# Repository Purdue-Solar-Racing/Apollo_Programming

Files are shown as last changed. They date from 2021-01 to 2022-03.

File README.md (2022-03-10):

# Apollo_Programming
Purdue Solar main code repository for the Apollo car. 

## Subsystem Hardware Status
Status Key and Due Dates
0. Not Started
1. Started in Research
2. In Schematic Work
3. Schematic Finished - Oct 23rd, 2021
4. PCB Layout Finished - Nov 13/20th, 2021
5. Manufactuing Stage
6. Debugged and Working

| Subsystem | Lead | Status | Members | Notes |
|---|---|---|---|---|
| Battery Protection System | Nate Nauman | 2/3 | Nicholas Gildenhuys | |
| Driver Display | Rachael Getz | 1 | Darin Tsai, Jing Hoon | |
| Light Controller | Darin Tsai | 3 | | |
| Junction Controller | Nicholas Gildenhuys | 0 | | |
| Motor Controller | Nate Nauman | 2 | Nicholas Gildenhuys | |
| Solar Array Controller | Landon Lindsay | 3 | Dhanu De Silva, Jing Hoon | |
| Vehicle Controller | Roshni Sharma | 2/3 | | |
| Wheel Controller | Nicholas Gildenhuys | 3 | | |

## Subsystem Software Status
Status Key:
0. Not Started
1. Started in Research
2. Prelim Code
3. Main Functions Built Out
4. Integration Stage
5. Integration Finished

| Subsystem | Lead | Status | Members | Notes |
|---|---|---|---|---|
| Battery Protection System | | 0 | 			 | |
| Driver Display | 			 | 0 | | |
| Light Controller | 		 | 0 | | |
| Junction Controller | 			 | 0 | | |
| Motor Controller | 		 | 0 | 			 | |
| Solar Array Controller | 		 | 0 | 			 | |
| Vehicle Controller | 		 | 0 | | |
| Wheel Controller | 			 | 0 | | |

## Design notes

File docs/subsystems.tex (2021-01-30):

\documentclass[letterpaper,12pt]{article}
\usepackage{amsmath, amssymb, geometry, amsfonts, graphicx}
\graphicspath{{./}}
\usepackage[shortlabels]{enumitem}
\usepackage{multicol}
\usepackage{hyperref}

\geometry{left=1in, right=1in, top=1in, bottom=1in}

\title{Purdue Solar Racing Apollo Electrical Susystems}
\author{Nicholas Gildenhuys}
\begin{document}

\maketitle
\tableofcontents
\newpage

\section{Battery Protection Controller}
   Main Function: Protect batteries and relay information fo the telemetry and driver display boards.  
   \subsection{Board I/O}
   \begin{multicols}{2}
   \flushleft{\textbf{Inputs:}}
   
   \flushleft{CAN:}
   \begin{itemize}
      \item Init Startup
   \end{itemize}
      
   \flushleft{Hardware:}
   \begin{itemize}
      \item Battery terminals
      \item Thermal sensor
      \item Voltage Sensor
      \item Aux Voltage
   \end{itemize}
   
   \columnbreak
   
   \flushleft{\textbf{Outputs:}}

   \flushleft{CAN:}
   \begin{itemize}
      \item Board Ready
      \item Battery Themperature
      \item Battery Capacity
   \end{itemize}
   
   \flushleft{Hardware:}
   \begin{itemize}
      \item Protected battery output
   \end{itemize}
   \end{multicols}
   % ARM-Cortex M1 Chip needed inputs and outputs
   \subsection{Processor Ports}
   \begin{multicols}{2}
   \begin{enumerate}[(a.)]
      \item power/ground
      \item CAN I/O network ports
      \item \# of thermistors
      \item \# Voltage info from IC
      
      \item CAN status
   \end{enumerate}
   \end{multicols}

\pagebreak
\section{Driver Display}
Main Function: Display all necessary info to the driver.
   \subsection{Board I/O}
   \begin{multicols}{2}
   \flushleft{\textbf{Inputs:}}
   
   \flushleft{CAN:}
   \begin{itemize}
      \item Init Startup
      \item All car signals
   \end{itemize}
   
   \flushleft{Hardware:}
   \begin{itemize}
      \item Aux Voltage
   \end{itemize}
   
   \columnbreak
   
   \flushleft{\textbf{Outputs:}}

   \flushleft{CAN:}
   \begin{itemize}
      \item Board Ready
   \end{itemize}
   
   \flushleft{Hardware:}
   \begin{itemize}
      \item LCD Display, if not actually integrated into the board
      \item Aux enable/kill?
   \end{itemize}
   \end{multicols}

   \subsection{Processor Ports}
   \begin{multicols}{2}
   \begin{enumerate}[(a.)]
      \item power/ground
      \item CAN I/O network ports 
   \columnbreak
      \item SPI output for display
      \item Logical out for another type display
      \item Multiplex line out for display
   \end{enumerate}
   \end{multicols}

\pagebreak
\section{Light Controller}
   Main Function: Take CAN messages input from driver controller to turn on lights  
   \subsection{Board I/O}
   \begin{multicols}{2}
   \flushleft{\textbf{Inputs:}}
   
   \flushleft{CAN:}
   \begin{itemize}
      \item Init Startup
      \item Turn Signals (2)
      \item Headlights
      \item Horn
      \item Windshield Wiper
   \end{itemize}
   
   \flushleft{Hardware:}
   \begin{itemize}
      \item Aux Voltage
   \end{itemize}
   
   \columnbreak
   
      \flushleft{\textbf{Outputs:}}

   \flushleft{CAN:}
   \begin{itemize}
      \item Board Ready
      \item Current Light Settings
   \end{itemize}
   
   \flushleft{Hardware:}
   \begin{itemize}
      \item Hardware inputs
      \item Power to lights, horn, and windshield wiper
      \item Control signal to windshield wiper
   \end{itemize}
   \end{multicols}

   \subsection{Processor Ports}
   \begin{multicols}{2}
   \begin{enumerate}[(a.)]
      \item power/ground
      \item CAN I/O network ports
      \item Switch to determine if it is a rear of front controller 
      
      \item \# PWM output for light controls 
   \end{enumerate}
   \end{multicols}

\pagebreak
\section{Junction (saftey) Controller}
   Main Function: Buck down the voltage for the low power system and safely turn on all the subsytems.
   \subsection{Board I/O}
   \begin{multicols}{2}
   \flushleft{\textbf{Inputs:}}
   
   \flushleft{CAN:}
   \begin{itemize}
      \item Init Startup
      \item Soft Start System
   \end{itemize}
   
   \flushleft{Hardware:}
   \begin{itemize}
      \item Protected battery voltage
      \item Aux Voltage
   \end{itemize}
   
   \columnbreak
   
   \flushleft{\textbf{Outputs:}}

   \flushleft{CAN:}
   \begin{itemize}
      \item Board Ready
      \item Current subsystems connected
   \end{itemize}
   
   \flushleft{Hardware:}
   \begin{itemize}
      \item Bucked down voltage 
   \end{itemize}
   \end{multicols}

   \subsection{Processor Ports}
   \begin{multicols}{2}
   \begin{enumerate}[(a.)]
      \item power/ground
      
   \end{enumerate}
   \end{multicols}

\pagebreak
\section{Motor Controller}
   \subsection{Board I/O}
   \begin{multicols}{2}
   \flushleft{\textbf{Inputs:}}
   
   \flushleft{CAN:}
   \begin{itemize}
      \item Forward/Reverse
      \item Cruise Control
      \item Desired Speed
   \end{itemize}
   
   \flushleft{Hardware:}
   \begin{itemize}
      \item Thermistor
      \item Hall effect sensor
      \item Aux Voltage   
   \end{itemize}
   
   \columnbreak
   
   \flushleft{\textbf{Outputs:}}

   \flushleft{CAN:}
   \begin{itemize}
      \item Board Ready
   \end{itemize}
   
   \flushleft{Hardware:}
   \begin{itemize}
      \item 3 Phase motor outputs
   \end{itemize}
   \end{multicols}

   \subsection{Motor Controller Processor Ports}
   \begin{multicols}{2}
   \begin{enumerate}[(a.)]
      \item power/ground
      \item CAN I/O network ports for control
      \item thermistor input from motor
      \item hall effect input from motor

      \item 3 PWM output for motor
      \item desired speed output via SPI
      \item current measurment output via SPI
      \item voltage measurment output via SPI
      \item SPI data output to controller 2
   \end{enumerate}
   \end{multicols}

\pagebreak

\pagebreak
\section{Solar Array Controller}
   Main Function: Let the rest of the system what's going on with the solar panel
   \subsection{Board I/O}
   \begin{multicols}{2}
   \flushleft{\textbf{Inputs:}}
   
   \flushleft{CAN:}
   \begin{itemize}
      \item Init Startup
      \item Mode of operation
   \end{itemize}
   
   Hardware:
   \begin{itemize}
      \item Solar array
      \item Aux Voltage
   \end{itemize}
   
   \columnbreak
   
   \flushleft{\textbf{Outputs:}}

   \flushleft{CAN:}
   \begin{itemize}
      \item Board Ready
      \item Solar array power
      \item conversion efficiency
   \end{itemize}

   \flushleft{Hardware:}
   \begin{itemize}
      \item Power out
   \end{itemize}
   \end{multicols}

   \subsection{Processor Ports}
   \begin{multicols}{2}
      \begin{enumerate}[(a.)]
      \item Power/ground
      \item CAN I/O networ ports
      \item \# Panel Voltage info
   \end{enumerate}
   \end{multicols}

\pagebreak
\section{Vehicle Controller}
Main Function: Multiplex through all the buttons on the driver wheel to check if any button has been pressed. Once a button has been pressed send proper CAN message.
   \subsection{Board I/O}
   \begin{multicols}{2}
   \flushleft{\textbf{Inputs:}}
   
   \flushleft{CAN:}
   \begin{itemize}
      \item Init Startup
   \end{itemize}
   
   \flushleft{Hardware:}
   \begin{itemize}
      \item Aux Voltage
      \item Muxed buttons
   \end{itemize}
   
   \columnbreak
   
   \flushleft{\textbf{Outputs:}}

   \flushleft{CAN:}
   \begin{itemize}
      \item Board Ready
      \item Button Status
   \end{itemize}
   
   \flushleft{Hardware:}
   \begin{itemize}
      \item Mux control
   \end{itemize}
   \end{multicols}

   \subsection{Processor Ports}
   \begin{multicols}{2}
   \begin{enumerate}[(a.)]
      \item power/ground
      \item CAN I/O network ports
      \item Button logic input

      \item Button mux select line output
   \end{enumerate}
   \end{multicols}

\pagebreak
\section{Wheel Controller}
Main Function: Multiplex through all the buttons on the driver wheel to check if any button has been pressed. Once a button has been pressed send proper CAN message.
   \subsection{Board I/O}
   \begin{multicols}{2}
   \flushleft{\textbf{Inputs:}}
   
   \flushleft{CAN:}
   \begin{itemize}
      \item Init Startup
   \end{itemize}
   
   \flushleft{Hardware:}
   \begin{itemize}
      \item Aux Voltage
      \item Muxed buttons
   \end{itemize}
   
   \columnbreak
   
   \flushleft{\textbf{Outputs:}}

   \flushleft{CAN:}
   \begin{itemize}
      \item Board Ready
      \item Button Status
   \end{itemize}
   
   \flushleft{Hardware:}
   \begin{itemize}
      \item Mux control
   \end{itemize}
   \end{multicols}

   \subsection{Processor Ports}
   \begin{multicols}{2}
   \begin{enumerate}[(a.)]
      \item power/ground
      \item CAN I/O network ports
      \item Button logic input

      \item Button mux select line output
   \end{enumerate}
   \end{multicols}

\pagebreak

\end{document}

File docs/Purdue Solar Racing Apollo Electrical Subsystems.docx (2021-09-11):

# Purdue Solar Racing Apollo Electrical Subsystems

September 11, 2021

# Battery Protection Controller

## Overview

Protects the batteries from overcharging and discharging. Also Keeps track of the battery capacity and charge level.

## Board I/O

Inputs | Outputs

CAN Network

Hardware

## Processor Ports

Port Number | Details
| Power/GND
| CAN I/O
| Thermistors
| Battery Voltage

## Schematic

# Driver Display Controller

## Overview

## Board I/O

Inputs | Outputs

CAN Network

Hardware

## Processor Ports

Port Number | Details
| Power/GND
| CAN I/O

## Schematic

# Front/Rear Light Controller

## Overview

## Board I/O

Inputs | Outputs

CAN Network

Hardware

## Processor Ports

Port Number | Details
| Power/GND
| CAN I/O

## Schematic

# Junction (Safety) Controller

## Overview

## Board I/O

Inputs | Outputs

CAN Network

Hardware

## Processor Ports

Port Number | Details
| Power/GND
| CAN I/O

## Schematic

# Motor Controller

## Overview

## Board I/O

Inputs | Outputs

CAN Network

Hardware

## Processor Ports

Port Number | Details
| Power/GND
| CAN I/O

## Schematic

# Solar Array Controller

## Overview

## Board I/O

Inputs | Outputs

CAN Network

Hardware

## Processor Ports

Port Number | Details
| Power/GND
| CAN I/O

## Schematic

# Vehicle Controller

## Overview

## Board I/O

Inputs | Outputs

CAN Network

Hardware

## Processor Ports

Port Number | Details
| Power/GND
| CAN I/O

## Schematic

# Wheel Controller

## Overview

## Board I/O

Inputs | Outputs

CAN Network

Hardware

## Processor Ports

Port Number | Details
| Power/GND
| CAN I/O

## Schematic

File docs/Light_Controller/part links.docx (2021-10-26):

LM3402 -

https://www.digikey.com/en/products/detail/texas-instruments/LM3402HVMRX-NOPB/1840670

Replace lm3409 with Max16822A

https://www.digikey.com/en/products/detail/maxim-integrated/MAX16822AASA%2B/1937621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

Horn- PANASONIC

https://www.digikey.com/en/products/detail/panasonic-electric-works/ACT112/644612

LIGHTS

: https://www.digikey.com/en/products/detail/luminus-devices-inc-[chp]/SST-90-W30M-F11-GK700/3821667?utm_adgroup=LED%20Lighting%20-%20White&utm_source=google&utm_medium=cpc&utm_campaign=Shopping_Product_Optoelectronics&utm_term=&utm_content=LED%20Lighting%20-%20White&gclid=CjwKCAjw5c6LBhBdEiwAP9ejGwjSwyw_Pj36DDAqlJS9f7JQ09KdmdRvnD9cRKxKz_GElcORu_SJHhoCVJMQAvD_BwE

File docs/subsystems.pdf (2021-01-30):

# Purdue Solar Racing Apollo Electrical Susystems

### Nicholas Gildenhuys

### January 24, 2021

## Contents

1 Battery Protection Controller | 2
2 Driver Display | 3
3 Light Controller | 4
4 Junction (saftey) Controller | 5
5 Motor Controller | 6
6 Solar Array Controller | 7
7 Vehicle Controller | 8
8 Wheel Controller | 9

## 1 Battery Protection Controller

Main Function: Protect batteries and relay information fo the telemetry and driver display boards.

### 1.1 Board I/O

Inputs:

CAN:

- Init Startup

Hardware:

- Battery terminals
- Thermal sensor
- Voltage Sensor
- Aux Voltage

Outputs:

CAN:

- Board Ready
- Battery Themperature
- Battery Capacity

Hardware:

- Protected battery output

### 1.2 Processor Ports

(a.) power/ground

(b.) CAN I/O network ports

(c.) # of thermistors

(d.) # Voltage info from IC

(e.) CAN status

## 2 Driver Display

Main Function: Display all necessary info to the driver.

### 2.1 Board I/O

Inputs:

CAN:

- Init Startup
- All car signals

Hardware:

- Aux Voltage

Outputs:

CAN:

- Board Ready

Hardware:

- LCD Display, if not actually integrated into the board
- Aux enable/kill?

### 2.2 Processor Ports

(a.) power/ground

(b.) CAN I/O network ports

(c.) SPI output for display

(d.) Logical out for another type display

(e.) Multiplex line out for display

## 3 Light Controller

Main Function: Take CAN messages input from driver controller to turn on lights

### 3.1 Board I/O

Inputs:

CAN:

- Init Startup
- Turn Signals (2)
- Headlights
- Horn
- Windshield Wiper

Hardware:

- Aux Voltage

Outputs:

CAN:

- Board Ready
- Current Light Settings

Hardware:

- Hardware inputs
- Power to lights, horn, and windshield wiper
- Control signal to windshield wiper

### 3.2 Processor Ports

(a.) power/ground

(b.) CAN I/O network ports

(c.) Switch to determine if it is a rear of front controller

(d.) # PWM output for light controls

## 4 Junction (saftey) Controller

Main Function: Buck down the voltage for the low power system and safely turn on all the subsytems.

### 4.1 Board I/O

Inputs:

CAN:

- Init Startup
- Soft Start System

Hardware:

- Protected battery voltage
- Aux Voltage

Outputs:

CAN:

- Board Ready
- Current subsystems connected

Hardware:

- Bucked down voltage

### 4.2 Processor Ports

(a.) power/ground

## 5 Motor Controller

### 5.1 Board I/O

Inputs:

CAN:
- Forward/Reverse
- Cruise Control
- Desired Speed

Hardware:
- Thermistor
- Hall effect sensor
- Aux Voltage

Outputs:

CAN:

- Board Ready

Hardware:

- 3 Phase motor outputs

### 5.2 Motor Controller Processor Ports

(a.) power/ground

(b.) CAN I/O network ports for control

(c.) thermistor input from motor

(d.) hall effect input from motor

(e.) 3 PWM output for motor

(f.) desired speed output via SPI

(g.) current measurment output via SPI

(h.) voltage measurment output via SPI

(i.) SPI data output to controller 2

## 6 Solar Array Controller

Main Function: Let the rest of the system what’s going on with the solar panel

### 6.1 Board I/O

Inputs:

CAN:

- Init Startup
- Mode of operation

Hardware:

- Solar array
- Aux Voltage

Outputs:

CAN:

- Board Ready
- Solar array power
- conversion efficiency

Hardware:

- Power out

### 6.2 Processor Ports

(a.) Power/ground

(b.) CAN I/O networ ports

(c.) # Panel Voltage info

## 7 Vehicle Controller

Main Function: Multiplex through all the buttons on the driver wheel to check if any button has been pressed. Once a button has been pressed send proper CAN message.

### 7.1 Board I/O

Inputs:

CAN:

- Init Startup

Hardware:

- Aux Voltage
- Muxed buttons

Outputs:

CAN:

- Board Ready
- Button Status

Hardware:

- Mux control

### 7.2 Processor Ports

(a.) power/ground

(b.) CAN I/O network ports

(c.) Button logic input

(d.) Button mux select line output

## 8 Wheel Controller

Main Function: Multiplex through all the buttons on the driver wheel to check if any button has been pressed. Once a button has been pressed send proper CAN message.

### 8.1 Board I/O

Inputs:

CAN:

- Init Startup

Hardware:

- Aux Voltage
- Muxed buttons

Outputs:

CAN:

- Board Ready
- Button Status

Hardware:

- Mux control

### 8.2 Processor Ports

(a.) power/ground

(b.) CAN I/O network ports

(c.) Button logic input

(d.) Button mux select line output

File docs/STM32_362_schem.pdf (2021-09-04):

8

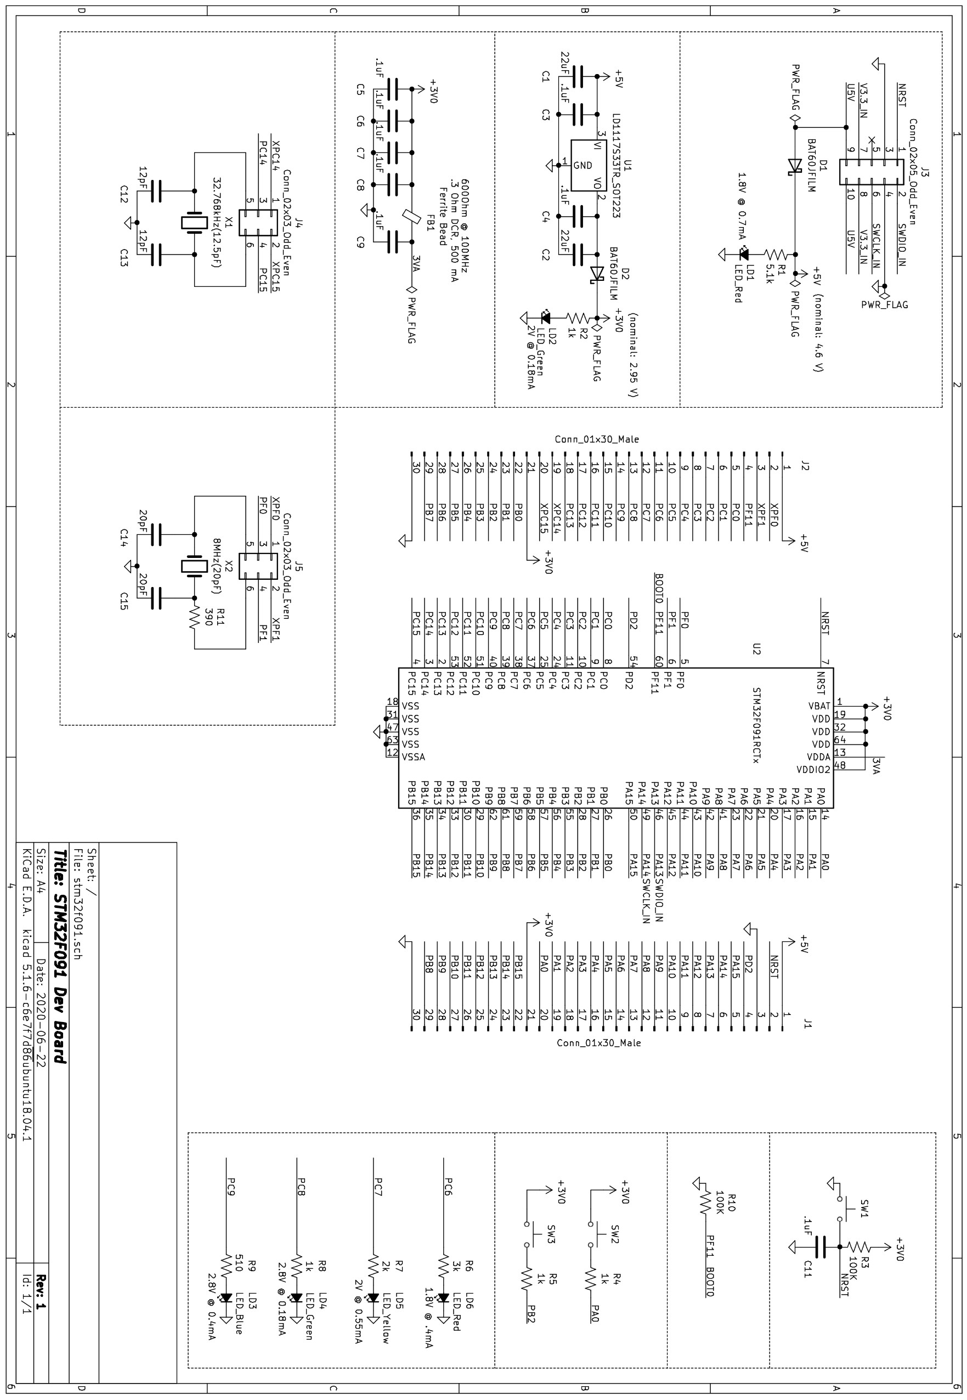
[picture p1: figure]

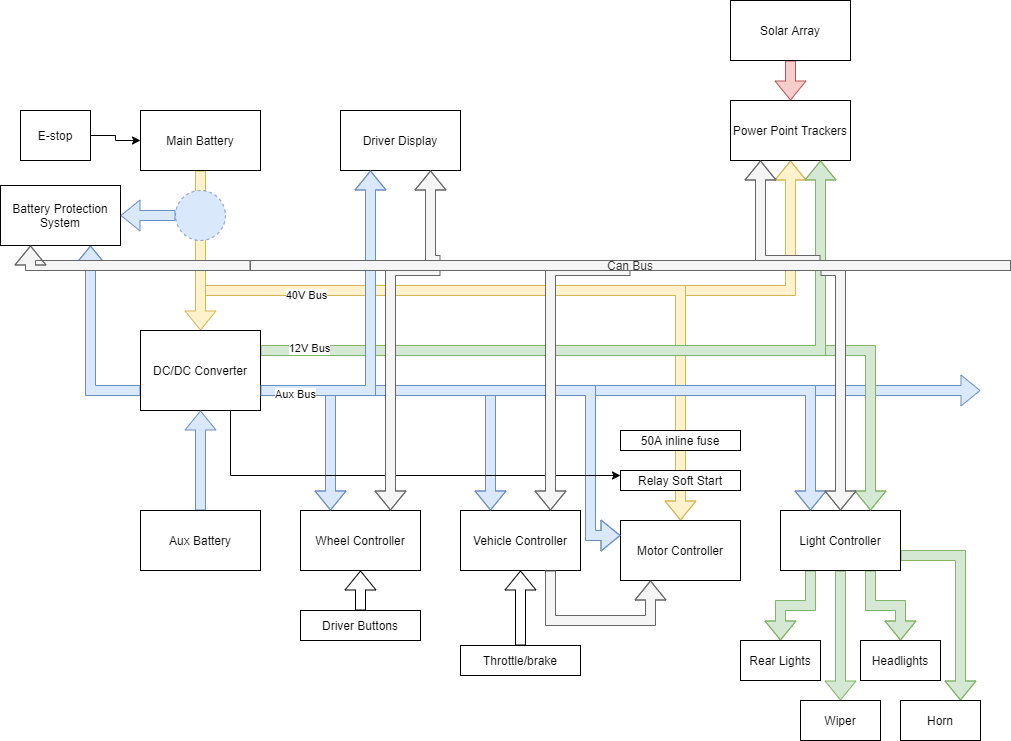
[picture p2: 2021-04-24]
docs/Apollo Power Diagram.png

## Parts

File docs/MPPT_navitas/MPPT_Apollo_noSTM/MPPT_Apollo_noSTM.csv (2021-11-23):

Reference | Quantity | Value | Footprint | Datasheet | Description | Height | Manufacturer_Name | Manufacturer_Part_Number | Part Number | Mouser Price/Stock | Arrow Part Number | Arrow Price/Stock
C27 | 1 | 0.1uF | Diode_SMD:D_SOD-123 | ~
C29 C31 C47 C50 C51 C52 C53 C54 C55 C58 C59 C60 C61 C62 C63 C64 C65 C66 C67 C68 C69 C70 C71 C72 C73 C74 C75 C76 C77 C78 C79 C80 C81 C82 C83 C84 | 36 | 2.2uF | CL05A225MQ5NNNC:CAPC1005X55N | ~ |  |  |  |  | CL05A225MQ5NNNC?
C30 C32 | 2 | 0.01uF | Capacitor_SMD:C_0805_2012Metric | ~
C28 C33 | 2 | 1uF | Capacitor_SMD:C_0805_2012Metric | ~
C35 C36 C37 C38 | 4 | 0.1uF | CL05A104KA5NNNC:CAPC1005X55N | ~
C34 C39 | 2 | 0.47uF | Capacitor_SMD:C_0805_2012Metric | ~
C42 C43 C44 C85 | 4 | 150pF | Capacitor_SMD:C_0805_2012Metric | ~
C45 C46 | 2 | 1000pF | Capacitor_SMD:C_0603_1608Metric | ~
C48 C49 | 2 | .01uF | Capacitor_SMD:C_0805_2012Metric | ~
C56 C57 | 2 | 470pF | Capacitor_SMD:C_0402_1005Metric | ~
C89 C99 | 2 | .1uF | CL05A104KA5NNNC:CAPC1005X55N | ~
C91 C92 | 2 | 10uF | Capacitor_SMD:C_1206_3216Metric | ~
D11 D16 | 2 | D_Schottky | fsv201:FSV10100V | ~ |  |  |  |  | FSV20120V?
D12 D13 D17 D18 D19 D20 | 6 | D_Schottky | DIOC1107X98:DIOC1107X98 | ~ |  |  |  |  | DFLS1200-7?
D14 D15 D21 D22 | 4 | D_Schottky | Diode_SMD:D_SOD-123 | ~ |  |  |  |  | ?NRVB130T1G?
D9 D10 | 2 | D_Schottky | Diode_SMD:D_SOT-23_ANK | ~ |  |  |  |  | ?BAT54-HE3-18?
F1 F2 | 2 | 10A | Fuse:Fuseholder_Cylinder-5x20mm_Schurter_0031_8201_Horizontal_Open | ~ |  |  |  |  | ?0031.8001?
J10 | 1 | Conn_01x03_Male | Connector_PinSocket_2.54mm:PinSocket_1x03_P2.54mm_Vertical | ~
J15 | 1 | Conn_01x03_Female | Connector_PinSocket_2.54mm:PinSocket_1x03_P2.54mm_Vertical | ~
J6 | 1 | PV | TerminalBlock_MetzConnect:TerminalBlock_MetzConnect_Type011_RT05502HBWC_1x02_P5.00mm_Horizontal | ~ |  |  |  |  | ?31055102?
J7 | 1 | BAT | TerminalBlock_MetzConnect:TerminalBlock_MetzConnect_Type011_RT05502HBWC_1x02_P5.00mm_Horizontal | ~ |  |  |  |  | ?31055102?
L4 | 1 | L_Core_Iron | SER2915L-682KL_KiCad:SER2915L682KL | ~ |  |  |  |  | SER2915L-682KL
Q1 Q3 Q4 Q5 Q6 | 5 | 2N7002 | Package_TO_SOT_SMD:SOT-23 | https://www.onsemi.com/pub/Collateral/NDS7002A-D.PDF |  |  |  |  | ?2N7002T?
Q2 | 1 | Q_NPN_BCE | Diode_SMD:D_SOT-23_ANK | ~ |  |  |  |  | ?MMBT4401-7-F?
R28 | 1 | 49.9 | Resistor_SMD:R_0603_1608Metric | ~
R29 R49 R55 | 3 | 19.1k | Resistor_SMD:R_0603_1608Metric | ~
R30 R32 R42 R43 R61 R62 | 6 | 2k | Resistor_SMD:R_0603_1608Metric | ~
R31 R38 R39 R40 R41 R44 R52 R53 R58 R71 R72 R77 R78 R79 R80 R82 R109 | 17 | 10k | Resistor_SMD:R_0603_1608Metric | ~
R33 | 1 | 178k | Resistor_SMD:R_0603_1608Metric | ~
R34 | 1 | 40.9k | Resistor_SMD:R_0603_1608Metric | ~
R35 | 1 | 1M | Resistor_SMD:R_0603_1608Metric | ~
R36 | 1 | 150k | Resistor_SMD:R_0603_1608Metric | ~
R37 | 1 | 45.3k | Resistor_SMD:R_0603_1608Metric | ~
R46 | 1 | 910k | Resistor_SMD:R_0603_1608Metric | ~
R47 R50 | 2 | 270k | Resistor_SMD:R_0603_1608Metric | ~
R51 | 1 | 340k | Resistor_SMD:R_0603_1608Metric | ~
R54 | 1 | 75k | Resistor_SMD:R_0603_1608Metric | ~
R56 R57 | 2 | 100k | Resistor_SMD:R_0603_1608Metric | ~
R59 R60 | 2 | 26.1k | Resistor_SMD:R_0603_1608Metric | ~
R63 | 1 | 698 | Resistor_SMD:R_0603_1608Metric | ~
R67 R68 | 2 | 0.004 | Resistor_SMD:R_2512_6332Metric | ~
R69 R70 R74 R75 R95 R96 R97 R98 | 8 | 10 | Resistor_SMD:R_0603_1608Metric | ~
R73 R76 | 2 | 4.99 | Resistor_SMD:R_0805_2012Metric | ~
R81 R83 | 2 | DNP | Resistor_SMD:R_0603_1608Metric | ~
R84 R85 | 2 | short | Resistor_SMD:R_0603_1608Metric | ~
R89 R90 R91 R92 R93 R94 | 6 | 0 | Resistor_SMD:R_0603_1608Metric | ~
U10 | 1 | Driver_FET_SM72295MA_Navitas | Package_SO:SOIC-28W_7.5x17.9mm_P1.27mm
U10A1 U10B1 | 2 | SM72375 | LMC6772QMM-NOPB:LMC6772QMM&slash_NOPB | https://pdf1.alldatasheet.com/datasheet-pdf/view/463780/TI1/SM72375.html | Analog Comparators | 1.09 | Texas Instruments | SM72375
U11A1 U11B1 | 2 | MCP602-I_SN | MCP602T-I_ST:Microchip-MCP602T-I_ST-0 | http://ww1.microchip.com/downloads/en/DeviceDoc/21314g.pdf | Dual lowpower op-amp,MCP602-I/SN SO8 | 1.75 | Microchip | MCP602-I/SN
U12 U13 | 2 | INA199A1DCKR_NAVITAS | INA214CIDCKR:INA214CIDCKR |  |  |  |  |  | ?INA214CIDCKR?
U8 | 1 | SM72442MT_NOPB_Navitas | SM72442MTE_NOPB:SOP65P640X120-28N

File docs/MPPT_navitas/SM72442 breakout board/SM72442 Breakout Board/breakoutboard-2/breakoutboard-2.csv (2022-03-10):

Source: | C:\Users\progu\OneDrive\Documents\Github\Apollo_Programming\docs\MPPT_navitas\SM72442 breakout board\SM72442 Breakout Board\breakoutboard-2\breakoutboard-2.sch
Date: | 1/15/2022 16:18
Tool: | Eeschema (5.1.10)-1
Generator: | C:\Program Files\KiCad\bin\scripting\plugins/bom_csv_grouped_by_value_with_fp.py
Component Count: | 114
Ref | Qnty | Value | Cmp name | Footprint | Description | Vendor
C27, | 1 | 0.1uF | C | Capacitor_SMD:C_0805_2012Metric | Unpolarized capacitor
C28, C33, | 2 | 1uF | C | Capacitor_SMD:C_0805_2012Metric | Unpolarized capacitor |  | transparent with 4
C34, C39, | 2 | 0.47uF | C | Capacitor_SMD:C_0805_2012Metric | Unpolarized capacitor |  | the transparent packaging with 6
C47, C50, C51, C52, C53, C54, C55, C58, C59, C60, C61, C62, C63, C64, C65, C66, C67, C68, C69, C70, C71, C72, C73, C74, C75, C76, C77, C78, C79, C80, C81, C82, C83, C84, | 34 | 2.2uF | C_Small | CL05A225MQ5NNNC:CAPC1005X55N | Unpolarized capacitor, small symbol |  | 6
C48, C49, | 2 | .01uF | C_Small | Capacitor_SMD:C_0805_2012Metric | Unpolarized capacitor, small symbol
C56, C57, | 2 | 470pF | C_Small | Capacitor_SMD:C_0402_1005Metric | Unpolarized capacitor, small symbol
C89, C99, | 2 | .1uF | C_Small | CL05A104KA5NNNC:CAPC1005X55N | Unpolarized capacitor, small symbol |  |  | C0805C104K1RACTM
C91, C92, | 2 | 10uF | C_Small | Capacitor_SMD:C_1206_3216Metric | Unpolarized capacitor, small symbol
D11, D16, | 2 | D_Schottky | D_Schottky | fsv201:FSV10100V | Schottky diode |  |  | RB218NS150TL
D12, D13, D17, D18, D19, D20, | 6 | Device_D_Schottky | Device_D_Schottky | DFLS1200-7:Diodes_Inc.-PowerDI123-03_2017-0-MFG
D14, | 1 | Device_D_Schottky | Device_D_Schottky | Diode_SMD:D_SOD-123
D15, D21, D22, | 3 | D_Schottky | D_Schottky | Diode_SMD:D_SOD-123 | Schottky diode
F1, F2, | 2 | 10A | Fuse | Fuse:Fuseholder_Cylinder-5x20mm_Schurter_0031_8201_Horizontal_Open | Fuse
J1, | 1 | PV_IN | Conn_01x01 | Connector_PinSocket_2.00mm:PinSocket_1x01_P2.00mm_Vertical | Generic connector, single row, 01x01, script generated (kicad-library-utils/schlib/autogen/connector/) |  |  |  | Ampere too big for connectors
J2, | 1 | Connector_Generic_Conn_01x02 | Connector_Generic_Conn_01x02 | Connector_PinSocket_2.00mm:PinSocket_1x02_P2.00mm_Vertical
J3, | 1 | Iin_sense_INA | Conn_01x03 | Connector_PinSocket_2.00mm:PinSocket_1x03_P2.00mm_Vertical | Generic connector, single row, 01x03, script generated (kicad-library-utils/schlib/autogen/connector/)
J4, | 1 | Iout_sense_INA | Conn_01x03 | Connector_PinSocket_2.00mm:PinSocket_1x03_P2.00mm_Vertical | Generic connector, single row, 01x03, script generated (kicad-library-utils/schlib/autogen/connector/)
J5, | 1 | Iin_sense | Conn_01x02 | Connector_PinSocket_2.00mm:PinSocket_1x02_P2.00mm_Vertical | Generic connector, single row, 01x02, script generated (kicad-library-utils/schlib/autogen/connector/)
J6, | 1 | PV | Conn_01x02 | TerminalBlock_MetzConnect:TerminalBlock_MetzConnect_Type011_RT05502HBWC_1x02_P5.00mm_Horizontal | Generic connector, single row, 01x02, script generated (kicad-library-utils/schlib/autogen/connector/)
J7, | 1 | BAT | Conn_01x02 | TerminalBlock_MetzConnect:TerminalBlock_MetzConnect_Type011_RT05502HBWC_1x02_P5.00mm_Horizontal | Generic connector, single row, 01x02, script generated (kicad-library-utils/schlib/autogen/connector/)
J8, | 1 | Iout_sense | Conn_01x02 | Connector_PinSocket_2.00mm:PinSocket_1x02_P2.00mm_Vertical | Generic connector, single row, 01x02, script generated (kicad-library-utils/schlib/autogen/connector/)
J9, | 1 | Vout | Conn_01x01 | Connector_PinSocket_2.00mm:PinSocket_1x01_P2.00mm_Vertical | Generic connector, single row, 01x01, script generated (kicad-library-utils/schlib/autogen/connector/)
J9-1, | 1 | Connector_Generic_Conn_01x05 | Connector_Generic_Conn_01x05 | Connector_PinSocket_2.00mm:PinSocket_1x05_P2.00mm_Vertical
J10, | 1 | 10V | Conn_01x01 | Connector_PinSocket_2.00mm:PinSocket_1x01_P2.00mm_Vertical | Generic connector, single row, 01x01, script generated (kicad-library-utils/schlib/autogen/connector/)
J11, | 1 | 5V_conn | Conn_01x01 | Connector_PinSocket_2.00mm:PinSocket_1x01_P2.00mm_Vertical | Generic connector, single row, 01x01, script generated (kicad-library-utils/schlib/autogen/connector/)
L4, | 1 | L_Core_Iron | L_Core_Iron | SER2915L-682KL_KiCad:SER2915L682KL | Inductor with iron core
Q3, Q4, Q5, Q6, | 4 | 2N7002 | 2N7002 | IRF8010STRLPBF:IRF8010STRLPBF | 0.115A Id, 60V Vds, N-Channel MOSFET, SOT-23
R44, R71, R72, R77, R78, R80, R82, | 7 | 10k | R_Small_US | Resistor_SMD:R_0603_1608Metric | Resistor, small US symbol
R59, R60, | 2 | 26.1k | R_Small_US | Resistor_SMD:R_0603_1608Metric | Resistor, small US symbol
R61, R62, | 2 | 2k | R_Small_US | Resistor_SMD:R_0603_1608Metric | Resistor, small US symbol
R67, R68, | 2 | 0.004 | R_Small_US | Resistor_SMD:R_2512_6332Metric | Resistor, small US symbol
R69, R70, R74, R75, R95, R96, R97, R98, | 8 | 10 | R_Small_US | Resistor_SMD:R_0603_1608Metric | Resistor, small US symbol
R73, R76, | 2 | 4.99 | R_Small_US | Resistor_SMD:R_0805_2012Metric | Resistor, small US symbol
R81, R83, | 2 | DNP | R_Small_US | Resistor_SMD:R_0603_1608Metric | Resistor, small US symbol
R84, R85, | 2 | short | R_Small_US | Resistor_SMD:R_0603_1608Metric | Resistor, small US symbol
R89, R90, R91, R92, R93, R94, | 6 | 0 | R_US | Resistor_SMD:R_0603_1608Metric | Resistor, US symbol
U10, | 1 | Driver_FET_SM72295MA_Navitas | Driver_FET_SM72295MA_Navitas | Package_SO:SOIC-28W_7.5x17.9mm_P1.27mm
U12, U13, | 2 | INA199A1DCKR_NAVITAS | INA199A1DCKR_NAVITAS | INA214CIDCKR:INA214CIDCKR

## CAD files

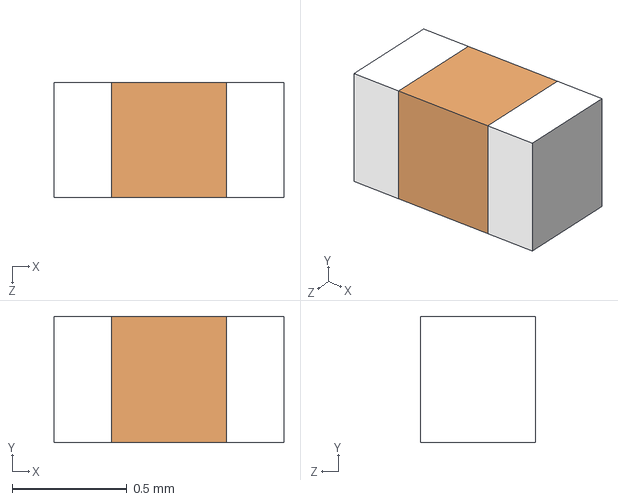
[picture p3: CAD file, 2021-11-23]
docs/MPPT_navitas/user_lib/CL05A225MQ5NNNC/CL05A225MQ5NNNC.step
1.00 x 0.55 x 0.5 mm

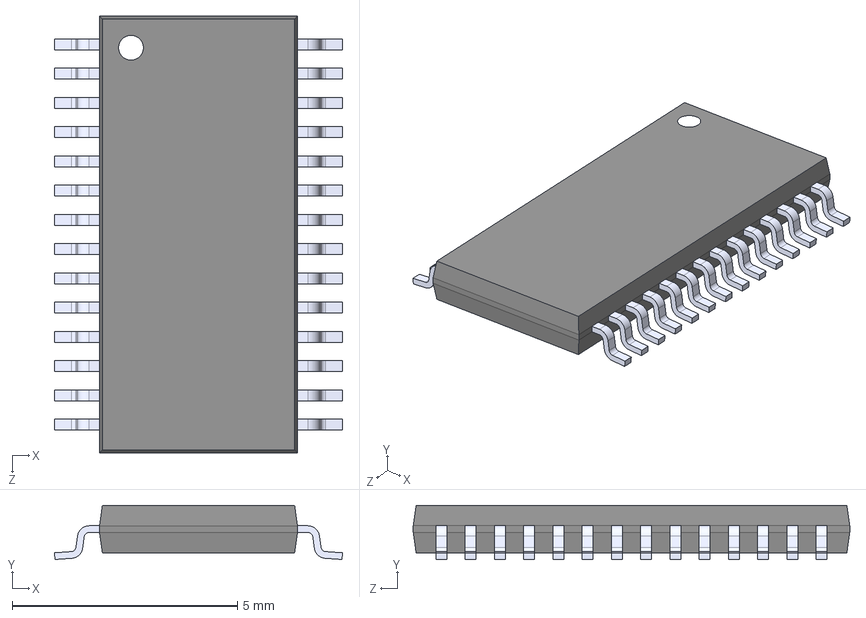
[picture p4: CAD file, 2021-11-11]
docs/MPPT_navitas/user_lib/SM72442MTE_NOPB/SM72442MTE_NOPB.step
6.40 x 1.20 x 9.70 mm

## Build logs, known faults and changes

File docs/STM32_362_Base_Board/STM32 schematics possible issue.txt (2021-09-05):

Possible issue:
1) Different types of LED were used. Schematics of the original PDF file uses
solid filled LED symbol whereas the newly created schematics uses a hollow LED symbol.

2)Specifications of LED, ferrite beadr and nominal voltage are added using 'Place text' tool. I am not
certain if that is the correct way of labeling the specifications.

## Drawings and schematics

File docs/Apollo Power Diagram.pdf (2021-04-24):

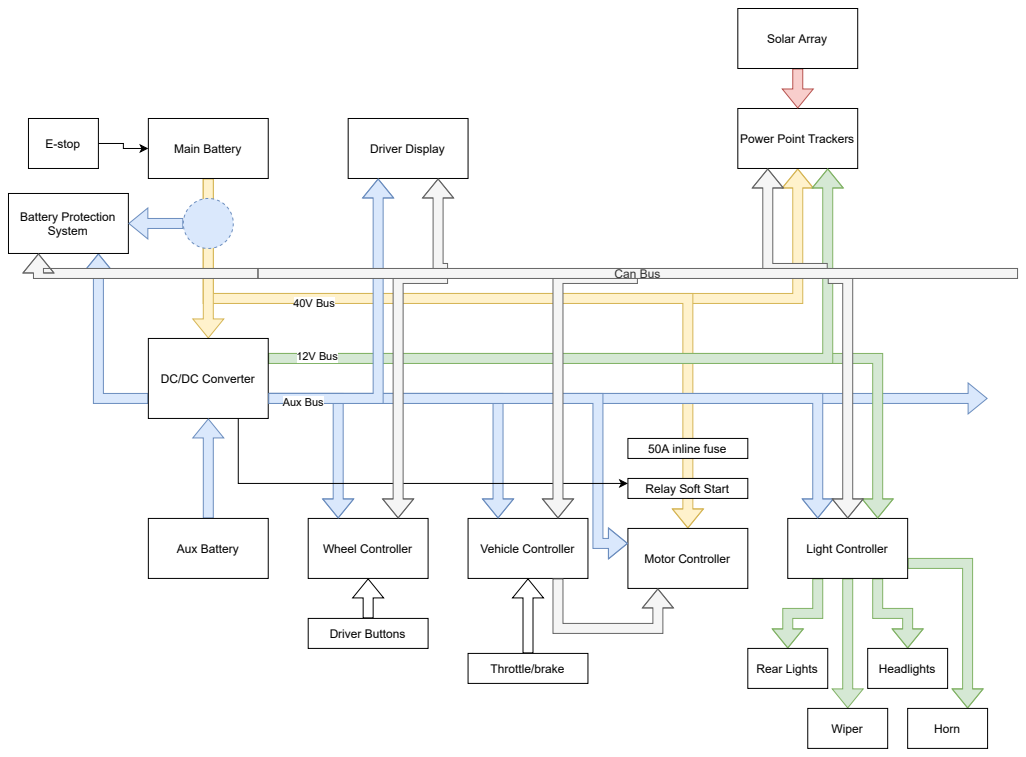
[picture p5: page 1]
40V Bus; Main Battery; Driver Display; Wheel Controller; Vehicle Controller; Light Controller; Motor Controller; 12V Bus; Aux Battery; Battery Protection System; E-stop; 50A inline fuse; Rear Lights; Headlights; Wiper; Horn; Aux Bus; Can Bus; Solar Array; Throttle/brake; Driver Buttons

Power Point Trackers

DC/DC Converter

Relay Soft Start

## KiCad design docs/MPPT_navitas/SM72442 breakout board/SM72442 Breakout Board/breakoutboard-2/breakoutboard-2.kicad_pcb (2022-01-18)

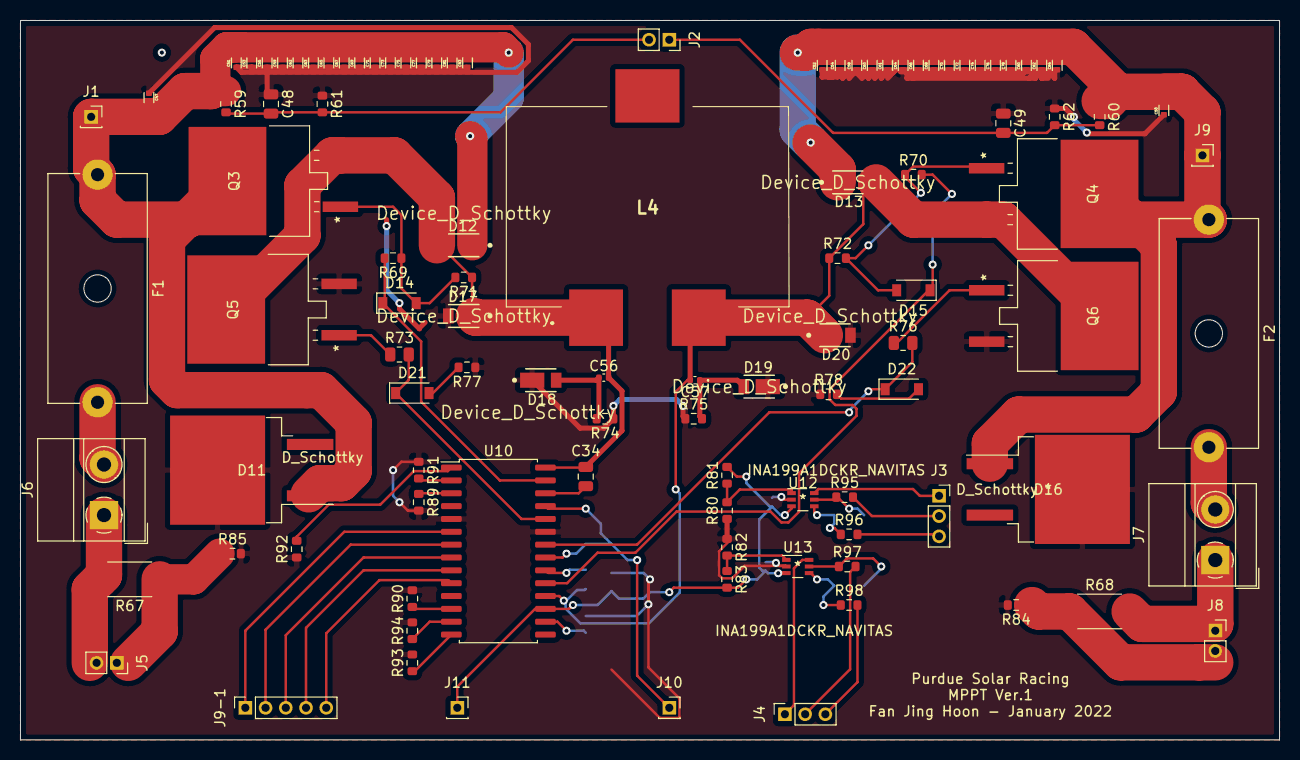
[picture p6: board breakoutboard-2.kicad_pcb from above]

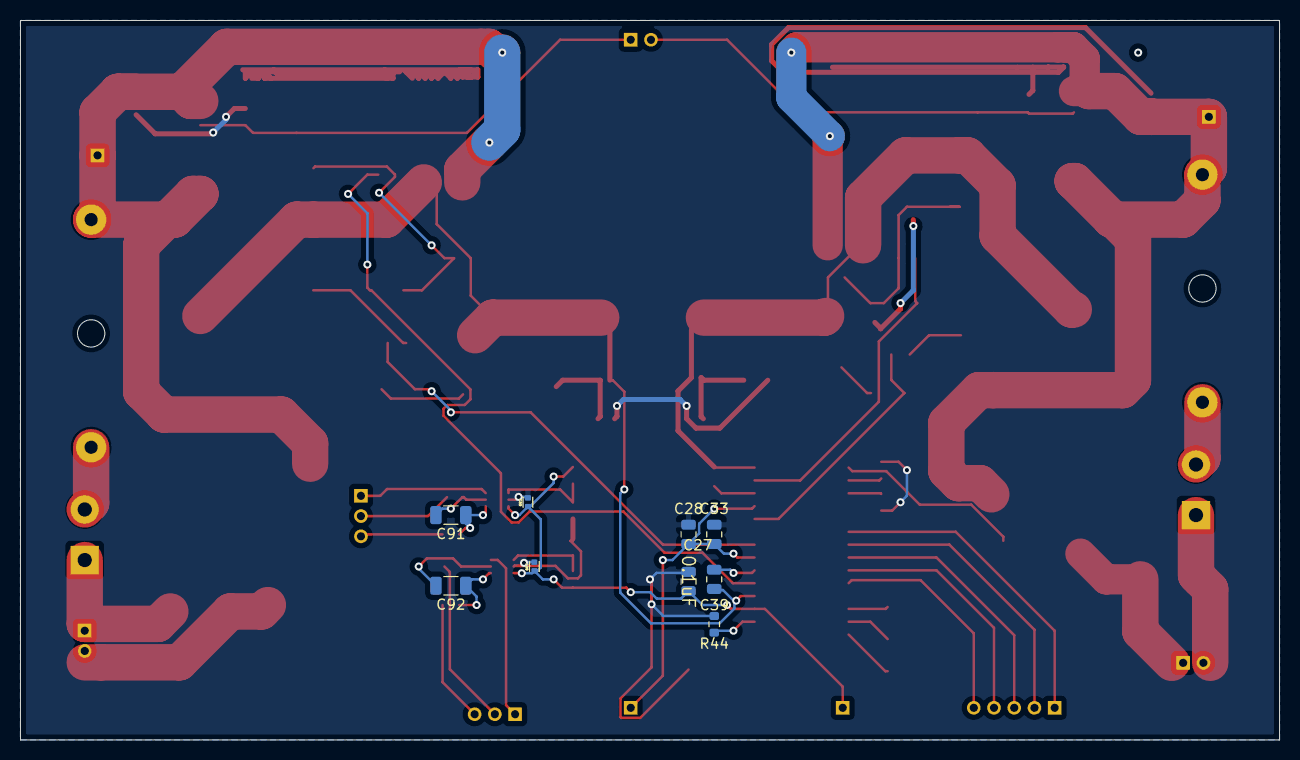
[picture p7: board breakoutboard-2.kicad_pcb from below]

Board: 2 copper layers, 124.5 x 71.1 mm, 114 parts (9 on the bottom side), 53 nets.

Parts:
C27: 0.1uF; C_0805_2012Metric
C28, C33: 1uF; C_0805_2012Metric
C34, C39: 0.47uF; C_0805_2012Metric
C47, C50, C51, C52, C53, C54, C55, C58, C59, C60, C61, C62, C63, C64, C65, C66, C67, C68, C69, C70, C71, C72, C73, C74, C75, C76, C77, C78, C79, C80, C81, C82, C83, C84: 2.2uF; CAPC1005X55N
C48, C49: .01uF; C_0805_2012Metric
C56, C57: 470pF; C_0402_1005Metric
C89, C99: .1uF; CAPC1005X55N
C91, C92: 10uF; C_1206_3216Metric
D11, D16: D_Schottky; TO-263-2
D12, D13, D17, D18, D19, D20: Device_D_Schottky; Diodes_Inc.-PowerDI123-03_2017-0-MFG
D14: Device_D_Schottky; D_SOD-123
D15, D21, D22: D_Schottky; D_SOD-123
F1, F2: 10A; Fuseholder_Cylinder-5x20mm_Schurter_0031_8201_Horizontal_Op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
J1: PV_IN; PinSocket_1x01_P2.00mm_Vertical
J2: Connector_Generic_Conn_01x02; PinSocket_1x02_P2.00mm_Vertical
J3: Iin_sense_INA; PinSocket_1x03_P2.00mm_Vertical
J4: Iout_sense_INA; PinSocket_1x03_P2.00mm_Vertical
J5: Iin_sense; PinSocket_1x02_P2.00mm_Vertical
J6: PV; TerminalBlock_MetzConnect_Type011_RT05502HBWC_1x02_P5.00mm_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
J7: BAT; TerminalBlock_MetzConnect_Type011_RT05502HBWC_1x02_P5.00mm_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
J8: Iout_sense; PinSocket_1x02_P2.00mm_Vertical
J9: Vout; PinSocket_1x01_P2.00mm_Vertical
J9-1: Connector_Generic_Conn_01x05; PinSocket_1x05_P2.00mm_Vertical
J10: 10V; PinSocket_1x01_P2.00mm_Vertical
J11: 5V_conn; PinSocket_1x01_P2.00mm_Vertical
L4: L_Core_Iron; SER2915L682KL
Q3, Q4, Q5, Q6: 2N7002; IRF8010STRLPBF
R44, R71, R72, R77, R78, R80, R82: 10k; R_0603_1608Metric
R59, R60: 26.1k; R_0603_1608Metric
R61, R62: 2k; R_0603_1608Metric
R67, R68: .004; R_2512_6332Metric
R69, R70, R74, R75, R95, R96, R97, R98: 10; R_0603_1608Metric
R73, R76: 4.99; R_0805_2012Metric
R81, R83: DNP; R_0603_1608Metric
R84, R85: short; R_0603_1608Metric
R89, R90, R91, R92, R93, R94: 0; R_0603_1608Metric
U10: Driver_FET_SM72295MA_Navitas; SOIC-28W_7.5x17.9mm_P1.27mm
U12, U13: INA199A1DCKR_NAVITAS; INA214CIDCKR

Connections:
+5V: C27.2, C89.1, C99.1, J11.1, R81.2, R83.2, U10.17, U12.3, U13.3
GND: C27.1, C28.2, C33.2, C47.1, C48.1, C49.1, C50.1, C51.1, C52.1, C53.1, C54.1, C55.1, C58.1, C59.1, C60.1, C61.1, C62.1, C63.1, C64.1, C65.1, C66.1, C67.1, C68.1, C69.1, C70.1, C71.1, C72.1, C73.1, C74.1, C75.1, C76.1, C77.1, C78.1, C79.1, C80.1, C81.1, C82.1, C83.1, C84.1, C89.2, C99.2, D11.2, D16.2, D17.2, D18.1, D19.1, D20.2, Q5.2, Q6.2, R44.1, R61.1, R62.1, R74.1, R75.1, R77.1, R78.1, R80.1, R82.1, R84.2, R85.2, R89.2, R90.2, R91.1, R92.1, R93.2, R94.2, U10.5, U10.23, U12.2, U13.2
HOA: D14.1, R69.2, U10.27
HOB: D15.1, R70.2, U10.19
HSA: C34.1, C56.2, D12.2, D17.1, L4.1, Q3.2, Q5.3, R71.1, U10.28
HSB: C39.1, C57.2, D13.2, D20.1, L4.2, Q4.2, Q6.3, R72.1, U10.18
Iin_Sense+: J5.1, R67.1, R85.1
Iin_Sense-: J5.2, J6.1, R67.2
Iout_Sense+: J7.1, J8.1, R68.2
Iout_Sense-: J8.2, R68.1, R84.1
LOA: D21.1, R73.2, U10.24
LOB: D22.1, R76.2, U10.22
unnamed: C28.1, C33.1, J10.1, U10.21, U10.25
unnamed: C34.2, U10.26
unnamed: C39.2, U10.20
unnamed: C47.2, C51.2, C53.2, C55.2, C59.2, C62.2, C63.2, C65.2, C67.2, C69.2, C71.2, C73.2, C75.2, C77.2, C79.2, C81.2, C83.2, D11.1, D12.1, F1.1, J1.1, Q3.3, R59.1
unnamed: C50.2, C52.2, C54.2, C58.2, C60.2, C61.2, C64.2, C66.2, C68.2, C70.2, C72.2, C74.2, C76.2, C78.2, C80.2, C82.2, C84.2, D13.1, D16.1, F2.1, J9.1, Q4.3, R60.1
unnamed: C56.1, D18.2, R74.2
unnamed: C57.1, D19.2, R75.2
unnamed: C91.1, R96.1, U12.4
unnamed: C91.2, R95.1, U12.5
unnamed: C92.1, R98.1, U13.4
unnamed: C92.2, R97.1, U13.5
unnamed: D14.2, Q3.1, R69.1, R71.2
unnamed: D15.2, Q4.1, R70.1, R72.2
unnamed: D21.2, R77.2
unnamed: D22.2, R78.2
unnamed: F1.2, J6.2
unnamed: F2.2, J7.2
unnamed: J3.1, U12.6
unnamed: J3.2, R95.2
unnamed: J3.3, R96.2
unnamed: J4.1, U13.6
unnamed: J4.2, R97.2
unnamed: J4.3, R98.2
unnamed: J9-1.1, U10.6
unnamed: J9-1.2, U10.7
unnamed: J9-1.3, U10.8
unnamed: J9-1.4, U10.9
unnamed: J9-1.5, U10.10
unnamed: Q5.1, R73.1
unnamed: Q6.1, R76.1
unnamed: R44.2, U10.16
unnamed: R80.2, R81.1, U12.1
unnamed: R82.2, R83.1, U13.1
unnamed: R89.1, U10.3
unnamed: R90.1, U10.12
unnamed: R91.2, U10.2
unnamed: R92.2, U10.1
unnamed: R93.1, U10.14
unnamed: R94.1, U10.13
Vin_Sense: C48.2, J2.2, R59.2, R61.2
Vout_Sense: C49.2, J2.1, R60.2, R62.2

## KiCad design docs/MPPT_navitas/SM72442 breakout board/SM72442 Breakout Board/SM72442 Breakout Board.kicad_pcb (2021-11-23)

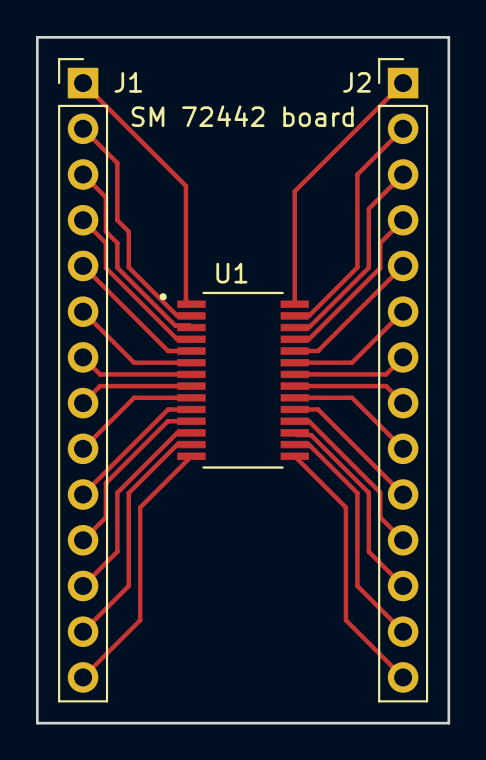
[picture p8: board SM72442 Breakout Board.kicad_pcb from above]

Board: 2 copper layers, 22.9 x 38.1 mm, 3 parts (0 on the bottom side), 28 nets.

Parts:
J1, J2: Conn_01x14_Male; PinHeader_1x14_P2.54mm_Vertical
U1: SM72442MT_NOPB; SOP65P640X120-28N

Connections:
/*RST: J1.1, U1.1
/A0: J1.14, U1.14
/A2: J2.13, U1.16
/A4: J2.11, U1.18
/A6: J2.9, U1.20
/AIIN: J2.10, U1.19
/AIOUT: J2.8, U1.21
/AVIN: J2.14, U1.15
/AVOUT: J2.12, U1.17
/HIA: J2.3, U1.26
/HIB: J2.4, U1.25
/I2C0: J1.6, U1.6
/I2C1: J1.7, U1.7
/I2C2: J2.7, U1.22
/LIA: J2.2, U1.27
/LIB: J2.5, U1.24
/NC1: J1.2, U1.2
/NC2: J1.5, U1.5
/NC3: J1.10, U1.10
/NC4: J2.6, U1.23
/PM: J2.1, U1.28
/PM_OUT: J1.11, U1.11
/SCL: J1.8, U1.8
/SDA: J1.9, U1.9
/VDDA: J1.12, U1.12
/VDDD: J1.3, U1.3
/VSSA: J1.13, U1.13
/VSSD: J1.4, U1.4

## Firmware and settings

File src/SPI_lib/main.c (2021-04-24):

/**
  ******************************************************************************
  * @file    main.c
  * @author  Ac6
  * @version V1.0
  * @date    01-December-2013
  * @brief   Default main function.
  ******************************************************************************
*/

//============================================================================
// ECE 362 lab experiment 8 -- SPI and DMA
//============================================================================

#include "stm32f0xx.h"
#include "lcd.h"
#include <stdio.h> // for sprintf()

// Be sure to change this to your login...
const char login[] = "ngildenh";

// Prototypes for misc things in lcd.c
void nano_wait(unsigned int);

// Write your subroutines below.

void setup_bb()
{
    // enable clock for port b
    RCC -> AHBENR |= RCC_AHBENR_GPIOBEN;
    // clear modes for pins 12, 13, 15
    GPIOB -> MODER &= ~(GPIO_MODER_MODER12 | GPIO_MODER_MODER13 | GPIO_MODER_MODER15);
    // set pin modes for pins 12, 13, 15 as general output
    GPIOB -> MODER |= GPIO_MODER_MODER12_0 | GPIO_MODER_MODER13_0 | GPIO_MODER_MODER15_0;
    // set the SCK low
    GPIOB -> ODR &= ~GPIO_ODR_13;
    // set the NSS high
    GPIOB -> ODR |= GPIO_ODR_12;

}

void small_delay()
{
    nano_wait(10000000);
}

void bb_write_bit(int bit)
{
    // set the MOSI pin to the value of that parameter
    if(bit)
        GPIOB -> ODR |= GPIO_ODR_15;
    else
        GPIOB -> ODR &= ~GPIO_ODR_15;
    // wait a small delay
    small_delay();
    // set the SCK high
    GPIOB -> ODR |= GPIO_ODR_13;
    // small delay
    small_delay();
    // set the SCK bit low
    GPIOB -> ODR &= ~GPIO_ODR_13;

}

void bb_write_byte(int byte)
{
    // write each bit in the byte to the MOSI pin, from MSB to LSB
    for(int i = 7; i >= 0; i--)
        bb_write_bit((byte >> i) & 0x1);
}

void bb_cmd(int cmd)
{
    // set NSS pin low
    GPIOB -> ODR &= ~GPIO_ODR_12;
    small_delay();

    bb_write_bit(0); // RS is 0 to start a command

    bb_write_bit(0); // R/W is 0 for a write

    bb_write_byte(cmd); // write the passed command byte

    small_delay();
    GPIOB -> ODR |= GPIO_ODR_12; // set the NSS bit high
    small_delay();
}

void bb_data(int data)
{
    // set NSS pin low
    GPIOB -> ODR &= ~GPIO_ODR_12;
    small_delay();

    bb_write_bit(1); // RS is 0 to start a command

    bb_write_bit(0); // R/W is 0 for a write

    bb_write_byte(data); // send the byte of data passed

    small_delay();
    GPIOB -> ODR |= GPIO_ODR_12; // set the NSS bit high
    small_delay();
}

void bb_init_oled()
{
    nano_wait(1000000); // wait for 1 millisecond
    // set the display for 8 bit operation
    bb_cmd(0x38);
    // turn the display off
    bb_cmd(0x08);
    // clear the display
    bb_cmd(0x01);

    nano_wait(2000000);

    // Set the display to scroll
    bb_cmd(0x06);
    // Move the cursor to home position
    bb_cmd(0x02);
    // turn the display on
    bb_cmd(0x0c);

}

void bb_display1(const char * string)
{
    bb_cmd(0x02); // move the cursor to home
    if(string != NULL){
        int i = 0;
        while(string[i] != '\0')
        {
            bb_data(string[i]);
            i++;
        }
    }
}


void bb_display2(const char * string)
{
    // move cursor to the lower row (offset 0x40)
    bb_cmd(0xc0);
    if(string != NULL)
    {
        int i = 0;
        while(string[i] != '\0')
        {
            bb_data(string[i]);
            i++;
        }
    }
}

void setup_spi2()
{
    RCC -> AHBENR |= RCC_AHBENR_GPIOBEN;
    // clear modes for pins 12, 13, 15
    GPIOB -> MODER &= ~(GPIO_MODER_MODER12 | GPIO_MODER_MODER13 | GPIO_MODER_MODER15);
    // set pin modes for pins 12, 13, 15 as general output
    GPIOB -> MODER |= GPIO_MODER_MODER12_1 | GPIO_MODER_MODER13_1 | GPIO_MODER_MODER15_1;
    // set the alternate function for PB12, 13, and 15 to NSS, SCk, and MOSI respectively
    GPIOB -> AFR[1] &= ~(GPIO_AFRH_AFR12 | GPIO_AFRH_AFR13 | GPIO_AFRH_AFR15);

    // enable the clock for the SPI2 subsystem
    RCC -> APB1ENR |= RCC_APB1ENR_SPI2EN;
    // set the BIDI mode to one line bidirectional
    // set the BIDIOE to enable output (transmit only mode)
    // set the BR  bits to 111 the the slowest baud rate
    // set the subsystem to master mode
    SPI2 -> CR1 |= SPI_CR1_BIDIMODE | SPI_CR1_BIDIOE | SPI_CR1_BR | SPI_CR1_MSTR;
    // set the SS output enable
    // enable the NSSP
    // set word size to 10-bit, DS[3:0] = 1001
    SPI2 -> CR2 = SPI_CR2_SSOE | SPI_CR2_NSSP | SPI_CR2_DS_3 | SPI_CR2_DS_0;
    // enable the SPI2
    SPI2 -> CR1 |= SPI_CR1_SPE;
}


void spi_cmd(int cmd)
{
    // wait for the transmit enable flag is set
    while(((SPI2 -> SR) & SPI_SR_TXE) == 0);
    // load the command into the data register
    SPI2 -> DR = cmd;
    // let the hardware do the rest
}


void spi_data(int data)
{
    // wait for the transmit enable flag to be set
    while(((SPI2 -> SR) & SPI_SR_TXE) == 0);
    // load the data into the data register,
    // but make sure the RS bit is set for the 10-bit word size
    SPI2 -> DR = data + 0x200;
}

void spi_init_oled()
{
    nano_wait(1000000);
    // set the display for 8 bit operation
    spi_cmd(0x38);
    // turn the display off
    spi_cmd(0x08);
    // clear the display
    spi_cmd(0x01);

    nano_wait(2000000);

    // Set the display to scroll
    spi_cmd(0x06);
    // Move the cursor to home position
    spi_cmd(0x02);
    // turn the display on
    spi_cmd(0x0c);
}
void spi_display1(const char * string)
{
    spi_cmd(0x02); // move the cursor to home
    if(string != NULL){
        int i = 0;
        while(string[i] != '\0')
        {
            spi_data(string[i]);
            i++;
        }
    }
}
void spi_display2(const char * string)
{
    // move cursor to the lower row (offset 0x40)
    spi_cmd(0xc0);
    if(string != NULL)
    {
        int i = 0;
        while(string[i] != '\0')
        {
            spi_data(string[i]);
            i++;
        }
    }

}


void  spi_enable_dma(const short * mem)
{
    // enable the clock to the DMA controller
    RCC -> AHBENR |= RCC_AHBENR_DMA1EN;
    DMA1_Channel5 -> CCR &= ~DMA_CCR_EN; // turn off the DMA
    // Set peripheral data register address to be the SPI2 DR
    DMA1_Channel5 -> CPAR = (uint32_t) (&(SPI2 -> DR));
    // Set the memory address to be the parameter passed
    DMA1_Channel5 -> CMAR = (uint32_t) (mem);
    // set the number of transfers to occur on channel 1 to be 34
    DMA1_Channel5 -> CNDTR = 34;
    // set direction to copy from memory to peripheral
    // set MINC to MINC to increment the CMAR for every transfer
    DMA1_Channel5 -> CCR |= DMA_CCR_DIR | DMA_CCR_MINC |
                            DMA_CCR_MSIZE_0 | DMA_CCR_PSIZE_0 | DMA_CCR_CIRC;
    // enable the channel
    DMA1_Channel5 -> CCR |= DMA_CCR_EN;
    // enable the DMA trigger when TX is empty
    SPI2 -> CR2 |= SPI_CR2_TXDMAEN;

}


void setup_spi1()
{
    // turn on GPIO port A
    RCC -> AHBENR |= RCC_AHBENR_GPIOAEN;
    // set pins PA4, 5, and 7 to AF
    GPIOA -> MODER &= ~(GPIO_MODER_MODER4 | GPIO_MODER_MODER5 | GPIO_MODER_MODER7);
    GPIOA -> MODER |= GPIO_MODER_MODER4_1 | GPIO_MODER_MODER5_1 | GPIO_MODER_MODER7_1;
    // configure PA2 and 3 to be outputs
    GPIOA -> MODER &= ~(GPIO_MODER_MODER2 | GPIO_MODER_MODER3);
    GPIOA -> MODER |= GPIO_MODER_MODER2_0 | GPIO_MODER_MODER3_0;
    // enable clock for SPI1
    RCC -> APB2ENR |= RCC_APB2ENR_SPI1EN;
    // set the BIDI mode to one line bidirectional
    // set the BIDIOE to enable output (transmit only mode)
    // set the subsystem to master mode
    SPI1 -> CR1 |= SPI_CR1_BIDIMODE | SPI_CR1_BIDIOE | SPI_CR1_MSTR;
    SPI1 -> CR1 &= ~SPI_CR1_BR; // set baud rate as fast as possible

    // set the SS output enable
    // enable the NSSP
    // leave word size to default 8-bit
    SPI1 -> CR2 = SPI_CR2_SSOE | SPI_CR2_NSSP;
    // enable the SPI2
    SPI1 -> CR1 |= SPI_CR1_SPE;
}


// Write your subroutines above.

void show_counter(short buffer[])
{
    for(int i=0; i<10000; i++) {
        char line[17];
        sprintf(line,"% 16d", i);
        for(int b=0; b<16; b++)
            buffer[1+b] = line[b] | 0x200;
    }
}

void internal_clock();
void demo();
void autotest();

extern const Picture *image;

int main(void)
{
    //internal_clock();
    //demo();
    //autotest();

    setup_bb();
    bb_init_oled();
    bb_display1("Hello");
    bb_display2(login);

    setup_spi2();
    spi_init_oled();
    spi_display1("Hello again,");
    spi_display2(login);

    short buffer[34] = {
            0x02, // This word sets the cursor to the beginning of line 1.
            // Line 1 consists of spaces (0x20)
            0x220, 0x220, 0x220, 0x220, 0x220, 0x220, 0x220, 0x220,
            0x220, 0x220, 0x220, 0x220, 0x220, 0x220, 0x220, 0x220,
            0xc0, // This word sets the cursor to the beginning of line 2.
            // Line 2 consists of spaces (0x20)
            0x220, 0x220, 0x220, 0x220, 0x220, 0x220, 0x220, 0x220,
            0x220, 0x220, 0x220, 0x220, 0x220, 0x220, 0x220, 0x220,
    };

    spi_enable_dma(buffer);
    show_counter(buffer);

    setup_spi1();
    LCD_Init();
    LCD_Clear(BLACK);
    LCD_DrawLine(10,20,100,200, WHITE);
    LCD_DrawRectangle(10,20,100,200, GREEN);
    LCD_DrawFillRectangle(120,20,220,200, RED);
    LCD_Circle(50, 260, 50, 1, BLUE);
    LCD_DrawFillTriangle(130,130, 130,200, 190,160, YELLOW);
    LCD_DrawChar(150,155, BLACK, WHITE, 'X', 16, 1);
    LCD_DrawString(140,60,  WHITE, BLACK, "ECE 362", 16, 0);
    LCD_DrawString(140,80,  WHITE, BLACK, "has the", 16, 1);
    LCD_DrawString(130,100, BLACK, GREEN, "best toys", 16, 0);
    LCD_DrawPicture(110,220,(const Picture *)&image);

}

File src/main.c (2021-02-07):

/**
  ******************************************************************************
  * @file    main.c
  * @author  Nicholas Gildenhuys
  * @version V1.0
  * @date    01-December-2013
  * @brief   Default main function.
  ******************************************************************************
*/


#include "stm32f0xx.h"
#include <stdint.h> // for uint8_t
#include "CANbx/bxcan.h"



int main(void)
{
    /* Initialization
     * init peripherals/ports 
     * init bxCAN
     * wait for interrupt from boot up signal
     * send boot up signal acknowledge
     */
    init_CAN_ports();
    init_bxCAN();
	for(;;)
	{
	    transmit_bxCAN(00, 'k');

	    /* poll for commands
	     * execute commands
	     * eventually want to make it interrupt driven so then its only
	     * wait for interrupt
	     * execute command
	     */

	}
}

/* main sequence for vehicle control unit
 * Initialize and check directly connected peripherals
 * initialize bxCAN
 * send out boot up command on the CAN network
 * wait for response, poll with timeout
 * take note of which peripheral is ready, turn on that light, and loop until
 * all peripherals are done booting up
 * main loop:
 * which takes in button commands and CAN commands
 * and relays them to the proper controller
 *
 */

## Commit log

2021-01-30 Init some button code
2021-02-07 Setup the eclipse project stuff
    [Apollo_Programming.cfg, Lab_Project.cfg]
2021-03-06 Most of Rick's board CADed up
    [STM32_Base_Board.kicad_pcb, STM32_Base_Board.sch]
2021-03-20 Initial Wheel controller finished, just need exact values and proper power routing
    [Button_Layout.sch, Can_Tranciever.sch, Processor.sch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]
2021-03-20 Initial commit for subsystem schematics
    [CAN_Traceiver.sch, CAN_Tranceiver.sch, Display.sch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]
2021-04-10 added lcd driver display info to schematic and symbol
    [CAN_Tranceiver.sch, Display.sch, Driver_Display.sch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]
2021-04-24 Additions to driver display, layed out all SPI signals.
    [Driver_Display.sch, Processor.sch]
2021-04-24 SPI prelim code examples from 362
2021-09-04 STM32 PDF Schematic Added
2021-09-04 Updated gitignore
    [Button_Layout.sch, CAN_Traceiver.sch, Can_Tranciever.sch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]
2021-09-05 The files are the replica of STM32 schematics with some concerns stated in the txt file
    [STM32_362.kicad_pcb, STM32_362.sch]
2021-09-25 Uploaded my schematics (wip)
    [lights.kicad_pcb, lights.sch]
2021-10-13 Create Vehicular Controller Subsystem.sch
    Starting phase of the Vehicular Controller Subsystem schematic with base board and digital pot.
    [Vehicular Controller Subsystem.sch]
2021-10-16 MPPT schematics file upload
    [MPPT_control_gate_drive.sch, MPPT_microcontrol_peri.sch, MPPT_navitas.kicad_pcb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]
2021-10-16 Update Vehicular Controller Subsystem.sch
    Placed Labels on pins that will need to be used for I2C.
    Added hierarchical pins on the base board sheet.
    [Vehicular Controller Subsystem.sch]
2021-10-16 Created power Electronics for mppt
    [lights.sch, power_Darin.kicad_pcb, power_Darin.sch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]
2021-10-23 update to hierarchical connection
    [MPPT_navitas.sch, STM32_MPPT.sch]
2021-10-23 update to hierarchical sheets location
    [MPPT_navitas.sch, MPPT_power_electronics.sch, MPPT_power_supplies.sch]
2021-10-23 update on stm32
    [STM32_MPPT.sch]
2021-10-23 Update STM32_MPPT.sch
    Test Push
    [STM32_MPPT.sch]
2021-10-23 Renaming redundant parts
    [MPPT_control_gate_drive.sch, MPPT_microcontrol_peri.sch, MPPT_power_electronics.sch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]
2021-10-23 updated stm32 in mppt
    [MPPT_control_gate_drive.sch, STM32_MPPT.sch]
2021-10-23 Finished, need Calculations
    [lights.sch, stm.sch]
2021-10-24 folder reordering
    [CAN_Traceiver.sch, Front_Light_Connections.sch, Light_Controller.kicad_pcb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]
2021-10-26 fixed some problem
    [MPPT_control_gate_drive.sch, MPPT_microcontrol_peri.sch, MPPT_power_electronics.sch]
2021-10-29 Throttle System V1
    [Throttle_Brake_Revised.sch]
2021-10-30 update on analog input pins
    [STM32_MPPT.sch]
2021-10-30 update on connection
    [MPPT_control.sch]
2021-11-06 Update on SM 72442 A0 resistance
    [MPPT_control.sch]
2021-11-11 Breakout board
    [SM72442 Breakout Board.kicad_pcb, SM72442 Breakout Board.sch, SM72442MTE_NOPB.step]
2021-11-13 breakout board update
    [MPPT_Apollo_noSTM.kicad_pcb, MPPT_Apollo_noSTM.sch, MPPT_control.sch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]
2021-11-23 relabel + recalc
    [lights.sch, stm.sch]
2021-11-23 update on PCB
    [CL05A225MQ5NNNC.step, MPPT_Apollo_noSTM.csv, MPPT_Apollo_noSTM.sch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]
2021-11-27 PCB update
    [MPPT_Apollo_noSTM.kicad_pcb, MPPT_Apollo_noSTM.sch, MPPT_control.sch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]
2021-12-07 Lighting Parts Footprints
    [lights.sch, stm.sch]
2022-01-03 update on pcb (in progress)
    [breakoutboard-2.kicad_pcb, breakoutboard-2.sch]
2022-01-06 PCB layout updated, next step to make traces & dimensions
    [breakoutboard-2.kicad_pcb]
2022-01-17 MPPT PCB completed, Gerber generated
    [breakoutboard-2-B_Cu.gbl, breakoutboard-2-B_Mask.gbs, breakoutboard-2-B_Paste.gbp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]
2022-01-18 footprint fixed, Gerber updated
    [breakoutboard-2-B_Cu.gbl, breakoutboard-2-B_Mask.gbs, breakoutboard-2-B_Paste.gbp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]
2022-03-10 update from some time ago
    [breakoutboard-2.csv]

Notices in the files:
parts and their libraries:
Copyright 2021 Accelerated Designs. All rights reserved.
